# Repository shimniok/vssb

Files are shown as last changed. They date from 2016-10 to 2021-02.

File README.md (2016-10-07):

A Vehicle Speed Sensor Buffer (VSSB) for GM Throttle Body Injection (TBI) ECM on my 86 Jeep
Grand Wagoneer.

The Jeep GW uses a VSS for cruise control that outputs 8-pulse (8000 pulses/mile) sine wave
This circuit and firmware convert the OEM VSS signal to a 2-pulse square wave 5V signal
compatible with the GM TBI ECM ('7747) that I'm using.

It also outputs a 4-pulse signal which would be used (I think) by electronic GM speedos. 
The GW speedo, of course, is mechanical.

So what's the advantage of having a working speed sensor? At least a couple of TBI features
are enabled. The ECM is able to distinguish between idle mode (vehicle speed < 4mph) and
throttle-off coasting.  Additionally, Deceleration Fuel Cut-Off (DCFO) mode is enabled in
part based on speed.  And, if enabled, lean highway cruise is based on speed as well.

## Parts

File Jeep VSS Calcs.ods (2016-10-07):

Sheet: Sheet1
Jeep VSS Calculations
Pulses / mile | 8000
mph | 1 | 2 | 4 | 6 | 8 | 10 | 20 | 40 | 60 | 80 | 100
Pulses / sec | 2.2 | 4.4 | 8.9 | 13.3 | 17.8 | 22.2 | 44.4 | 88.9 | 133.3 | 177.8 | 222.2
Measurements | Freq | Ampl
 | 10.0 | 0.8
 | 14.3 | 1.0
 | 25.0 | 1.8 |  |  |  |  |  |  |  |  |  | Cutoff at 50hz with 1st order filter means ½ gain at 100hz
 | 62.5 | 2.2 |  |  |  |  |  |  |  |  |  | R | 220 | K
 |  |  |  |  |  |  |  |  |  |  |  | Freq | 50
 | div | ms/div | div | v/div | freq | vpp |  |  |  |  |  | C | 0.0145 | uF
 | 5 | 10 | 1.8 | 0.5 | 20.0 | 0.9
 | 4 | 10 | 2 | 0.5 | 25.0 | 1.0
 | 3 | 10 | 2.4 | 0.5 | 33.3 | 1.2
 | 2 | 10 | 4 | 0.5 | 50.0 | 2.0
 | 3 | 5 | 5.2 | 0.5 | 66.7 | 2.6
 | 2.6 | 5 | 6 | 0.5 | 76.9 | 3.0
 | 1.6 | 5 | 4 | 1 | 125.0 | 4.0

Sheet: Sheet2
Schmitt Trigger Op Amp
Vcc | 5 | V
R1 | 330.0 | KΩ
R2 | 330.0 | KΩ
RFB | 330.0 | KΩ
R1||RFB (high) | 165.0 | KΩ
R2||RFB (low) | 165.0 | KΩ
Vhigh | 3.33 | V | 66.67%
Vlow | 1.67 | V | 33.33%

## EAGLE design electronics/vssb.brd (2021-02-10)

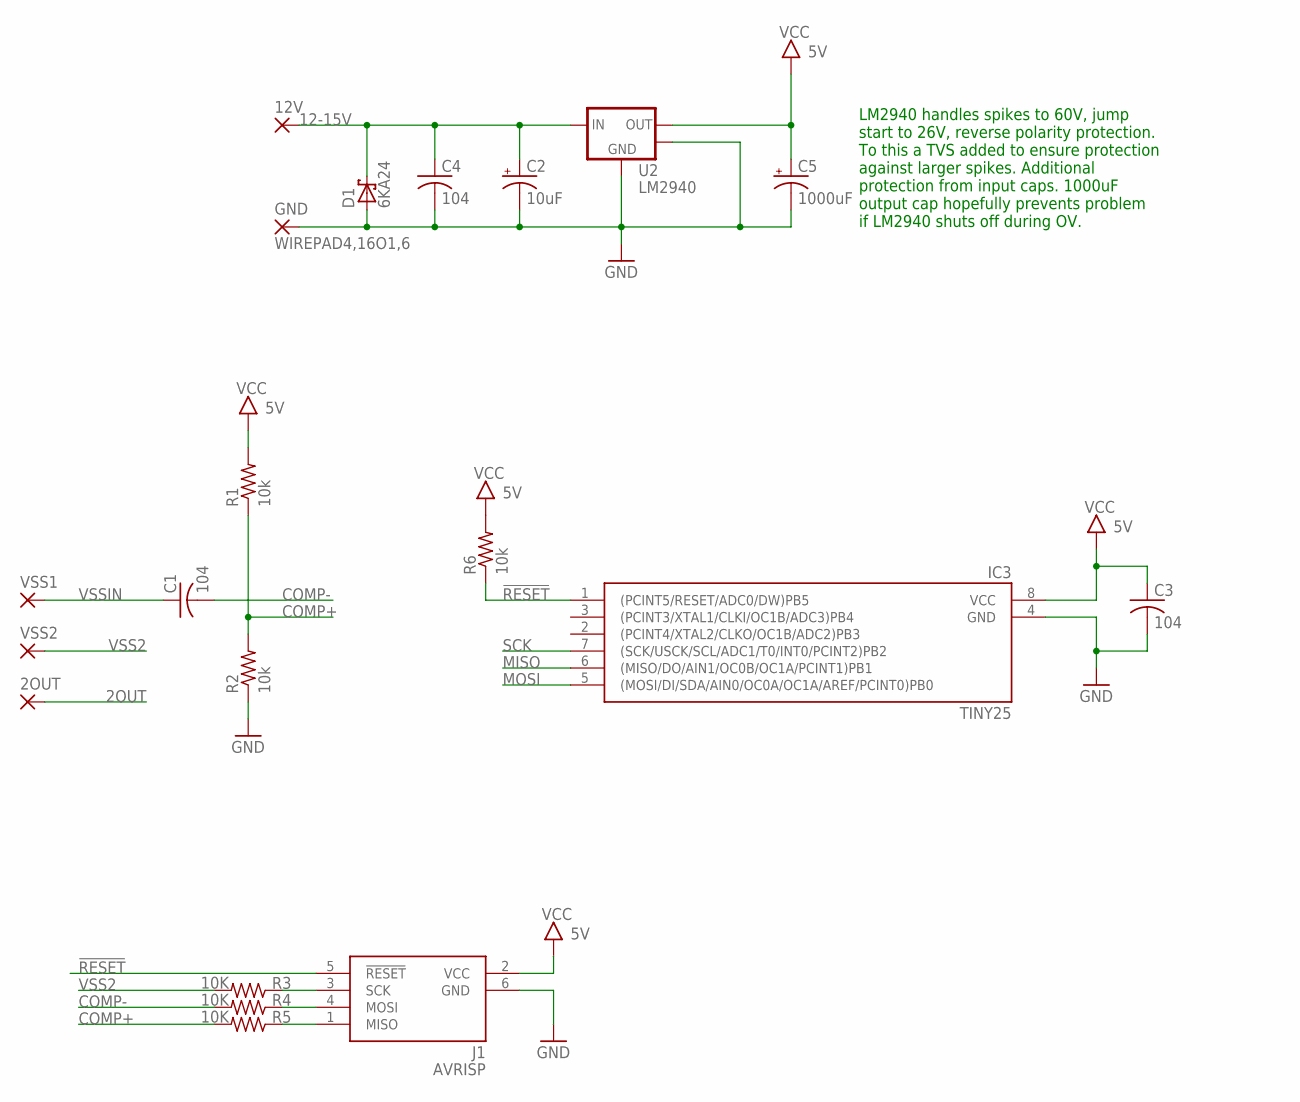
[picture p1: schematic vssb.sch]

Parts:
2OUT, 12V: WIREPAD4,16O1,6; 4,16O1,6
C1: 104; C050-024X044
C2: 10uF; E2,5-6
C3, C4: 104; C0603
C5: 1000uF; E5-13
D1: 6KA24; P600
GND: WIREPAD4,16O1,6; 4,16O1,6
IC3: TINY25; SOIC8N
J1: AVRISP; CON6P2R
R1, R2, R6: 10k; R0603
R3, R4, R5: 10K; R0603
U2: LM2940; SOT-223-3
VSS1, VSS2: WIREPAD4,16O1,6; 4,16O1,6

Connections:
2OUT: 2OUT.1
12-15V: 12V.1, C2.+, C4.1, D1.C, U2.1 (VIN)
!RESET: IC3.1 ((PCINT5/RESET/ADC0/DW)PB5), J1.5 (!RESET), R6.1
COMP+: R1.1, R2.2, R5.2
COMP-: C1.2, R4.2
GND: C2.-, C3.2, C4.2, C5.-, D1.A, GND.1, IC3.4 (GND), J1.6 (GND), R2.1, U2.2 (GND), U2.4 (TAB)
MISO: IC3.6 ((MISO/DO/AIN1/OC0B/OC1A/PCINT1)PB1), J1.1 (MISO), R5.1
MOSI: IC3.5 ((MOSI/DI/SDA/AIN0/OC0A/OC1A/AREF/PCINT0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), J1.4 (MOSI), R4.1
SCK: IC3.7 ((SCK/USCK/SCL/ADC1/T0/INT0/PCINT2)PB2), J1.3 (SCK), R3.1
VCC: C3.1, C5.+, IC3.8 (VCC), J1.2 (VCC), R1.2, R6.2, U2.3 (VOUT)
VSS2: R3.2, VSS2.1
VSSIN: C1.1, VSS1.1

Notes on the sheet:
LM2940 handles spikes to 60V, jump start to 26V, reverse polarity protection. To this a TVS added to ensure protection against larger spikes. Additional protection from input caps. 1000uF output cap hopefully prevents problem if LM2940 shuts off during OV.

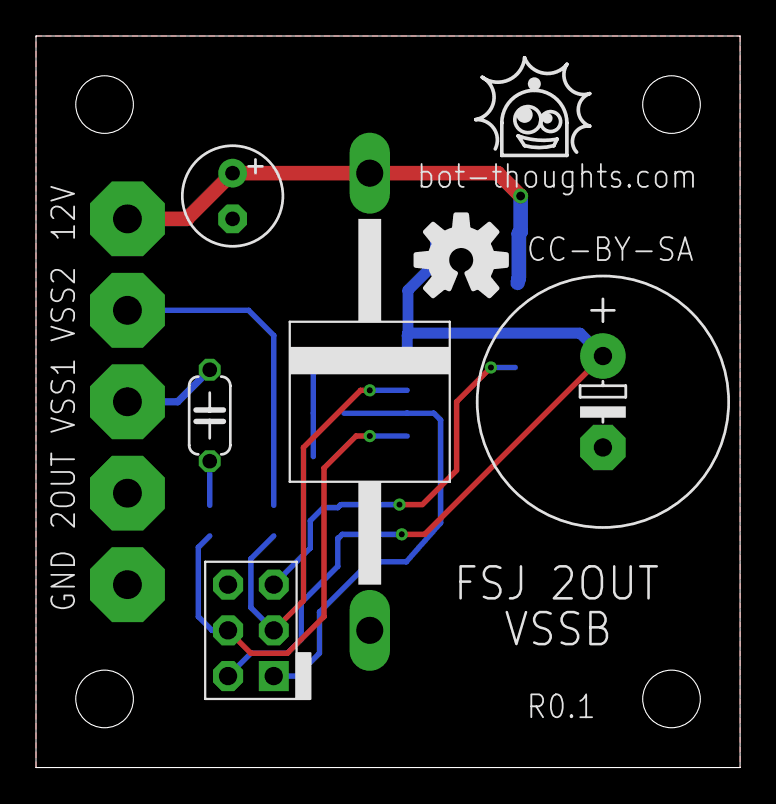
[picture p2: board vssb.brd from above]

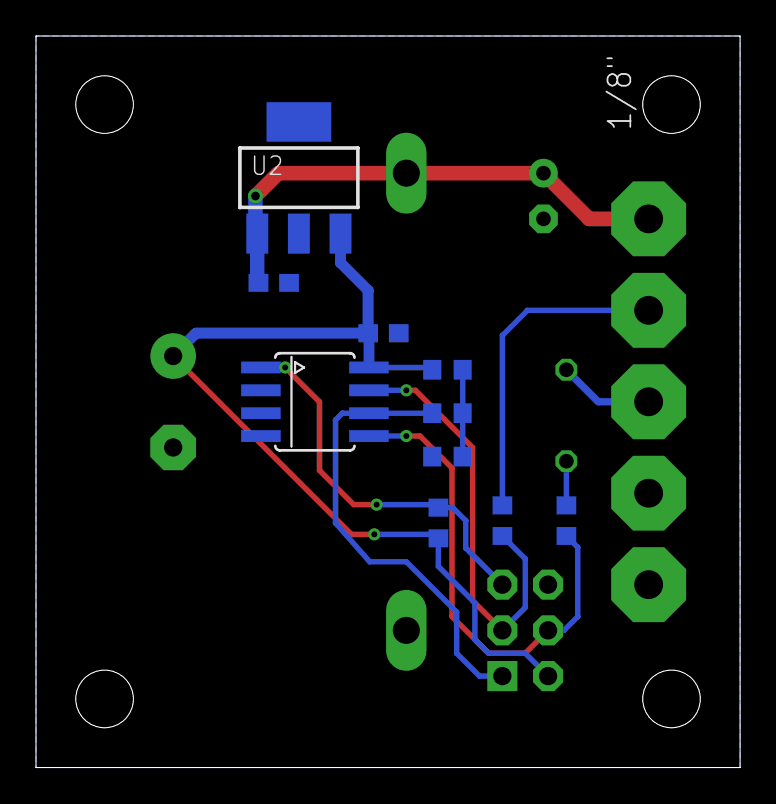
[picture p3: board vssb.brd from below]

Board: 2 copper layers, 39.1 x 40.6 mm, 20 parts (10 on the bottom side), 11 nets.

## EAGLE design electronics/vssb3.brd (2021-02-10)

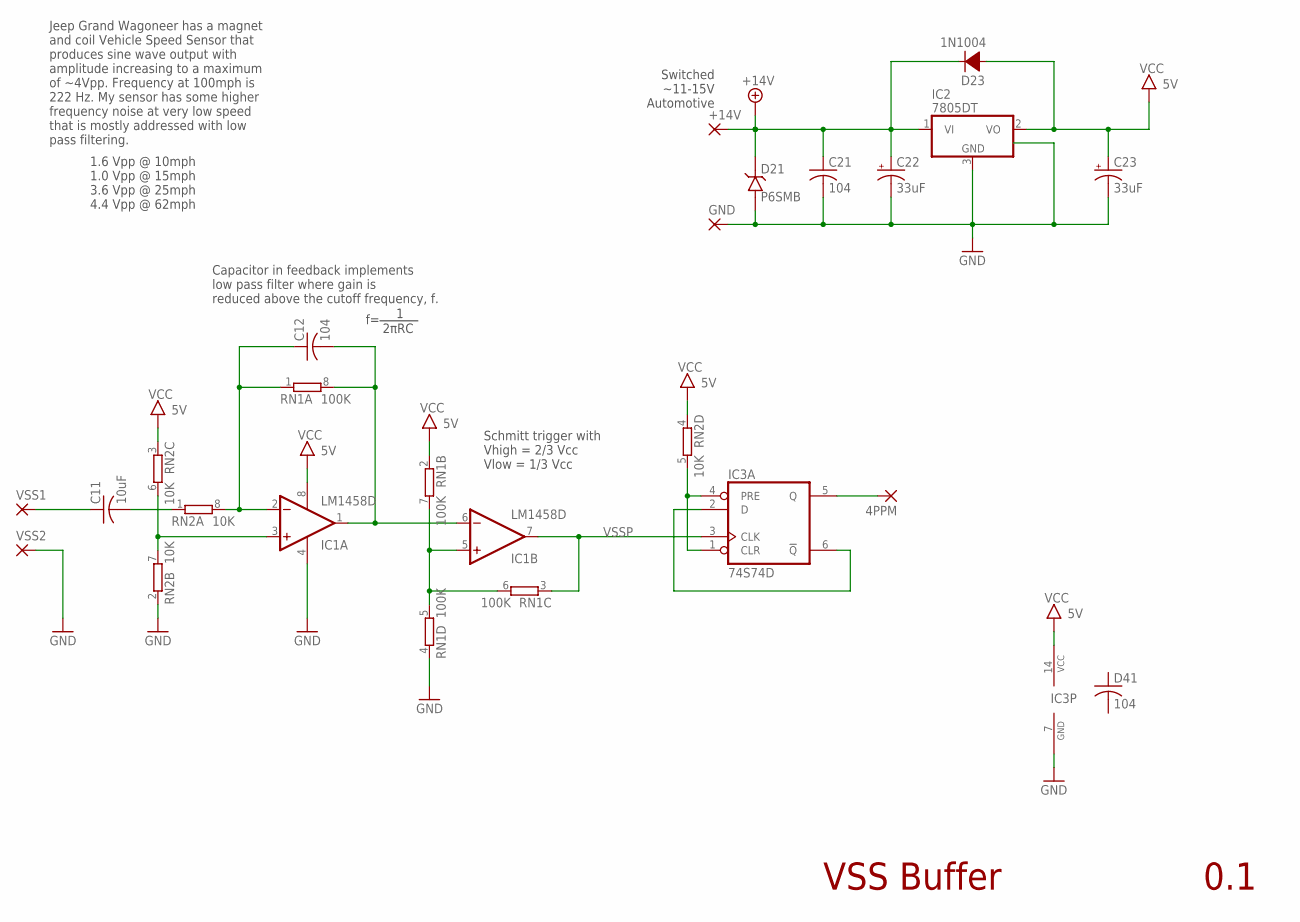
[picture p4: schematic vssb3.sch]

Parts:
4PPM: WIREPAD3,17/1,3; 3,17/1,3
+14V: WIREPAD3,17/1,3; 3,17/1,3
C11: 10uF; C1206
C12, C21: 104; C0603
C22, C23: 33uF; SMC_B
D21: P6SMB; DO-214AA
D23: 1N1004; SMA
D41: 104; C0603
GND: WIREPAD3,17/1,3; 3,17/1,3
IC1: LM1458D; SO08
IC2: 7805DT; TO252
IC3: 74S74D; SO14
RN1: 100K; EXB38V
RN2: 10K; EXB38V
VSS1, VSS2: WIREPAD3,17/1,3; 3,17/1,3

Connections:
4PPM: 4PPM.1, IC3.5 (Q)
+14V: +14V.1, C21.1, C22.+, D21.P$1 (C), D23.C, IC2.1 (VI)
GND: C21.2, C22.-, C23.-, D21.P$2 (A), GND.1, IC1.4 (V-), IC2.3 (GND), IC3.7 (GND), RN1.4 (1), RN2.2 (1), VSS2.1
unnamed: C11.2, RN2.1
unnamed: C12.1, IC1.2 (-IN), RN1.1, RN2.8 (2)
unnamed: IC1.3 (+IN), RN2.6 (2), RN2.7 (2)
unnamed: IC1.5 (+IN), RN1.5 (2), RN1.6 (2), RN1.7 (2)
unnamed: IC3.2 (D), IC3.6 (!Q)
unnamed: IC3.1 (CLR), IC3.4 (PRE), RN2.5 (2)
OUT1: C12.2, IC1.1 (OUT), IC1.6 (-IN), RN1.8 (2)
VCC: C23.+, D23.A, IC1.8 (V+), IC2.2 (VO), IC3.14 (VCC), RN1.2 (1), RN2.3 (1), RN2.4 (1)
VSS1: C11.1, VSS1.1
VSSP: IC1.7 (OUT), IC3.3 (CLK), RN1.3 (1)

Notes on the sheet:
Switched ~11-15V Automotive
Jeep Grand Wagoneer has a magnet and coil Vehicle Speed Sensor that produces sine wave output with amplitude increasing to a maximum of ~4Vpp. Frequency at 100mph is 222 Hz. My sensor has some higher frequency noise at very low speed that is mostly addressed with low pass filtering.
1.6 Vpp @ 10mph 1.0 Vpp @ 15mph 3.6 Vpp @ 25mph 4.4 Vpp @ 62mph
Capacitor in feedback implements low pass filter where gain is reduced above the cutoff frequency, f.
Schmitt trigger with Vhigh = 2/3 Vcc Vlow = 1/3 Vcc
2πRC
VSS Buffer
0.1

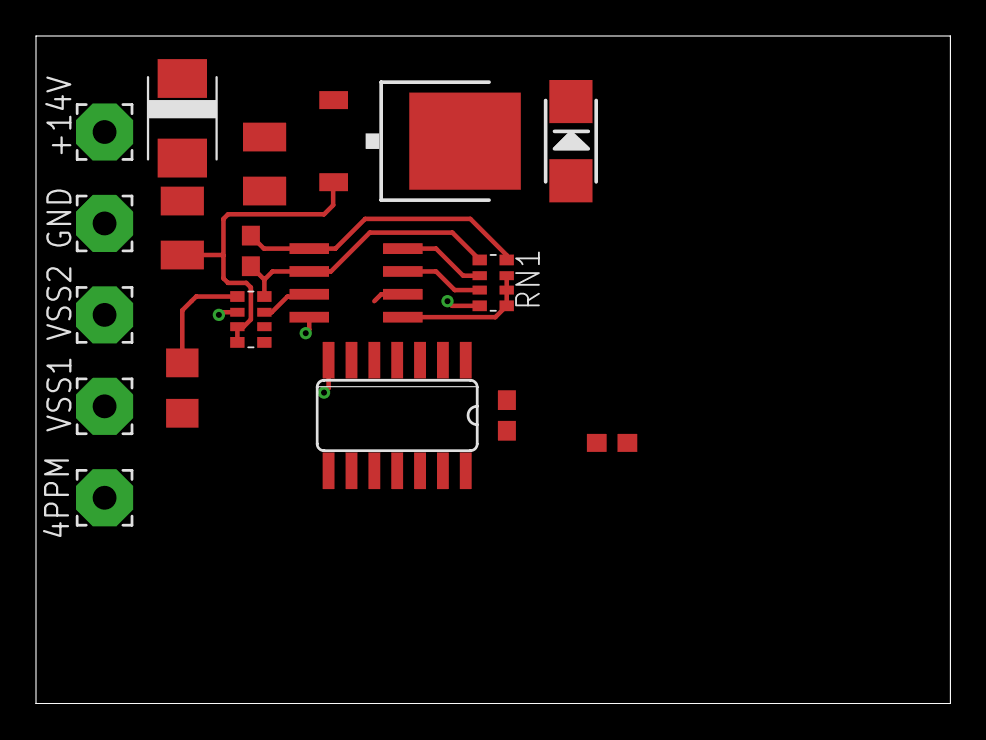
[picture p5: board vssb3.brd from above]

Board: 2 copper layers, 50.8 x 37.1 mm, 18 parts (0 on the bottom side), 13 nets.

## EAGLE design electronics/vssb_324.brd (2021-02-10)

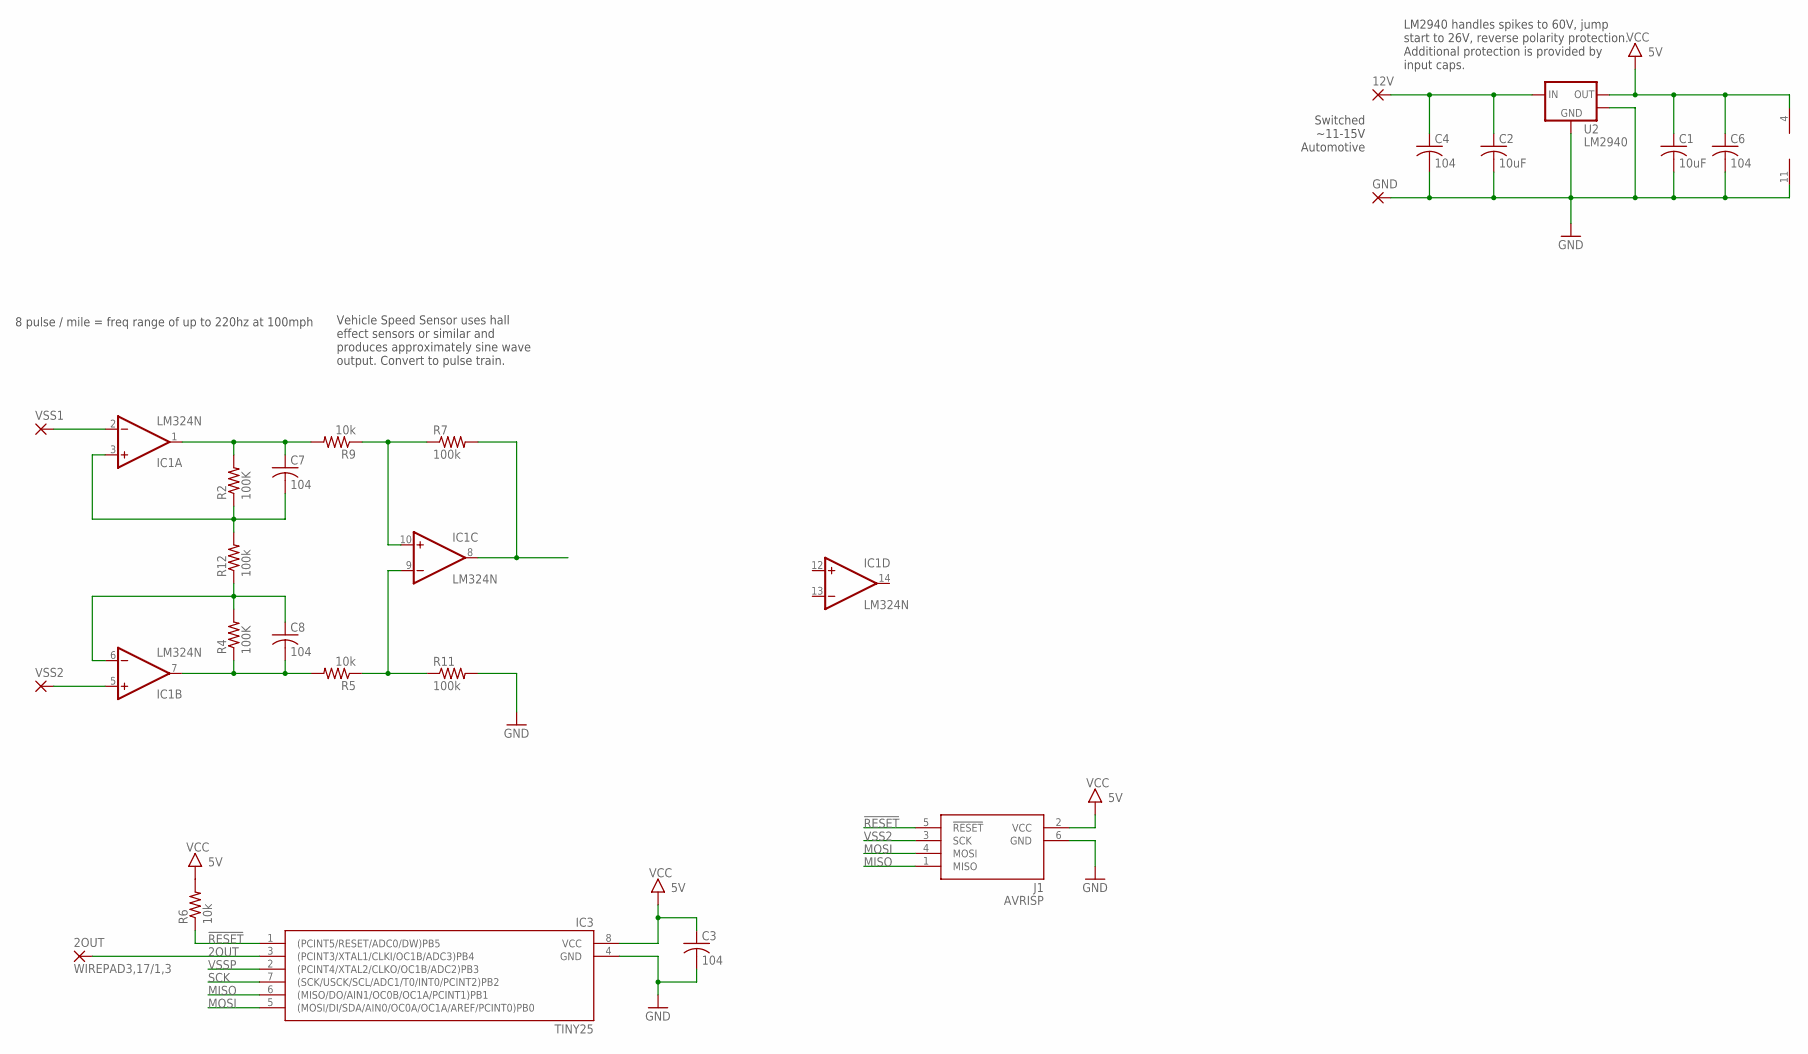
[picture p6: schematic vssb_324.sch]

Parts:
2OUT, 12V: WIREPAD3,17/1,3; 3,17/1,3
C1, C2: 10uF; C1206
C3, C4, C6, C7, C8: 104; C0603
GND: WIREPAD3,17/1,3; 3,17/1,3
IC1: LM324N; DIL14
IC3: TINY25; DIL08
J1: AVRISP; CON6P2R
R2, R4: 100K; R0603
R5, R6, R9: 10k; R0603
R7, R11, R12: 100k; R0603
U2: LM2940; TO263-3
VSS1, VSS2: WIREPAD3,17/1,3; 3,17/1,3

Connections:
2OUT: 2OUT.1, IC3.3 ((PCINT3/XTAL1/CLKI/OC1B/ADC3)PB4)
12-15V: 12V.1, C2.1, C4.1, U2.1 (VIN)
!RESET: IC3.1 ((PCINT5/RESET/ADC0/DW)PB5), J1.5 (!RESET), R6.1
GND: C1.2, C2.2, C3.2, C4.2, C6.2, GND.1, IC1.11 (V-), IC3.4 (GND), J1.6 (GND), R11.2, U2.2 (GND), U2.4 (TAB)
MISO: IC3.6 ((MISO/DO/AIN1/OC0B/OC1A/PCINT1)PB1), J1.1 (MISO)
MOSI: IC3.5 ((MOSI/DI/SDA/AIN0/OC0A/OC1A/AREF/PCINT0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), J1.4 (MOSI)
unnamed: C8.1, IC1.6 (-IN), R4.2, R12.1
unnamed: C7.2, IC1.3 (+IN), R2.1, R12.2
unnamed: IC1.8 (OUT), R7.2
unnamed: C7.1, IC1.1 (OUT), R2.2, R9.2
unnamed: C8.2, IC1.7 (OUT), R4.1, R5.2
unnamed: IC1.10 (+IN), R7.1, R9.1
unnamed: IC1.9 (-IN), R5.1, R11.1
SCK: IC3.7 ((SCK/USCK/SCL/ADC1/T0/INT0/PCINT2)PB2)
VCC: C1.1, C3.1, C6.1, IC1.4 (V+), IC3.8 (VCC), J1.2 (VCC), R6.2, U2.3 (VOUT)
VSS1: IC1.2 (-IN), VSS1.1
VSS2: IC1.5 (+IN), J1.3 (SCK), VSS2.1
VSSP: IC3.2 ((PCINT4/XTAL2/CLKO/OC1B/ADC2)PB3)

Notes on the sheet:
LM2940 handles spikes to 60V, jump start to 26V, reverse polarity protection. Additional protection is provided by input caps.
Switched ~11-15V Automotive
Vehicle Speed Sensor uses hall effect sensors or similar and produces approximately sine wave output. Convert to pulse train.
8 pulse / mile = freq range of up to 220hz at 100mph

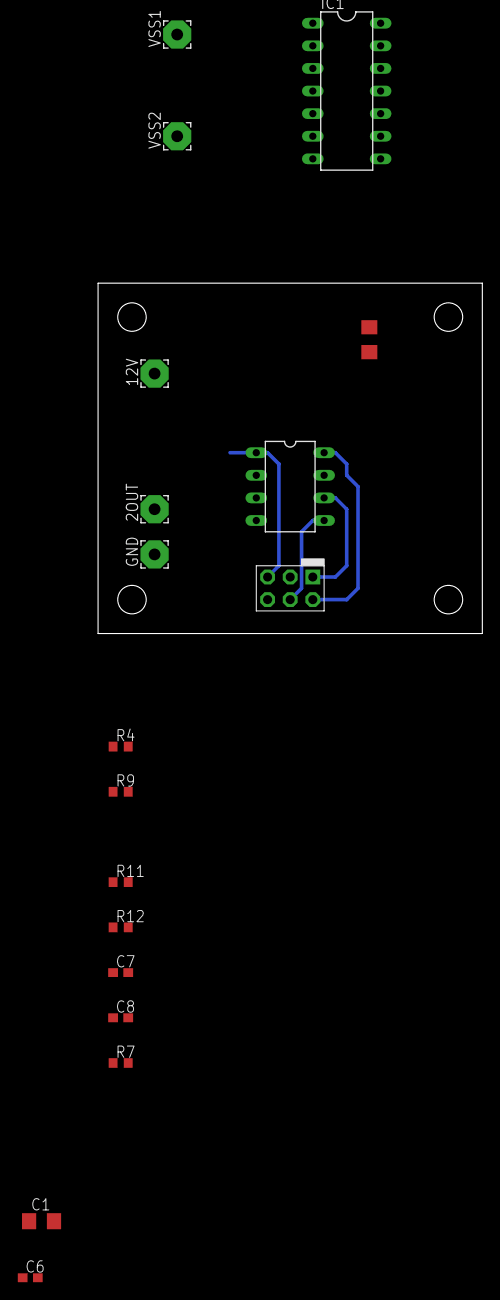
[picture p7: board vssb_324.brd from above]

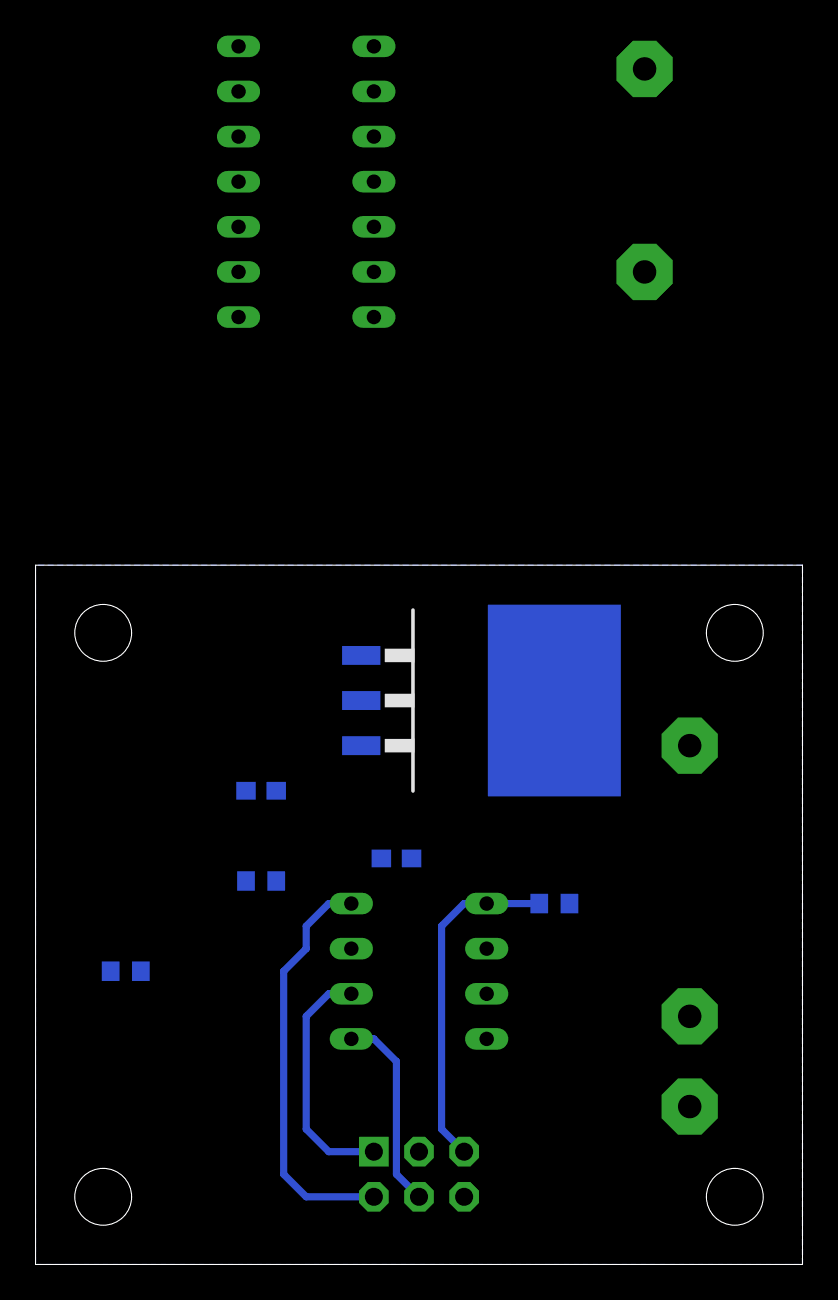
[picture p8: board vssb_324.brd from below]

Board: 2 copper layers, 43.2 x 39.4 mm, 24 parts (6 on the bottom side), 16 nets.

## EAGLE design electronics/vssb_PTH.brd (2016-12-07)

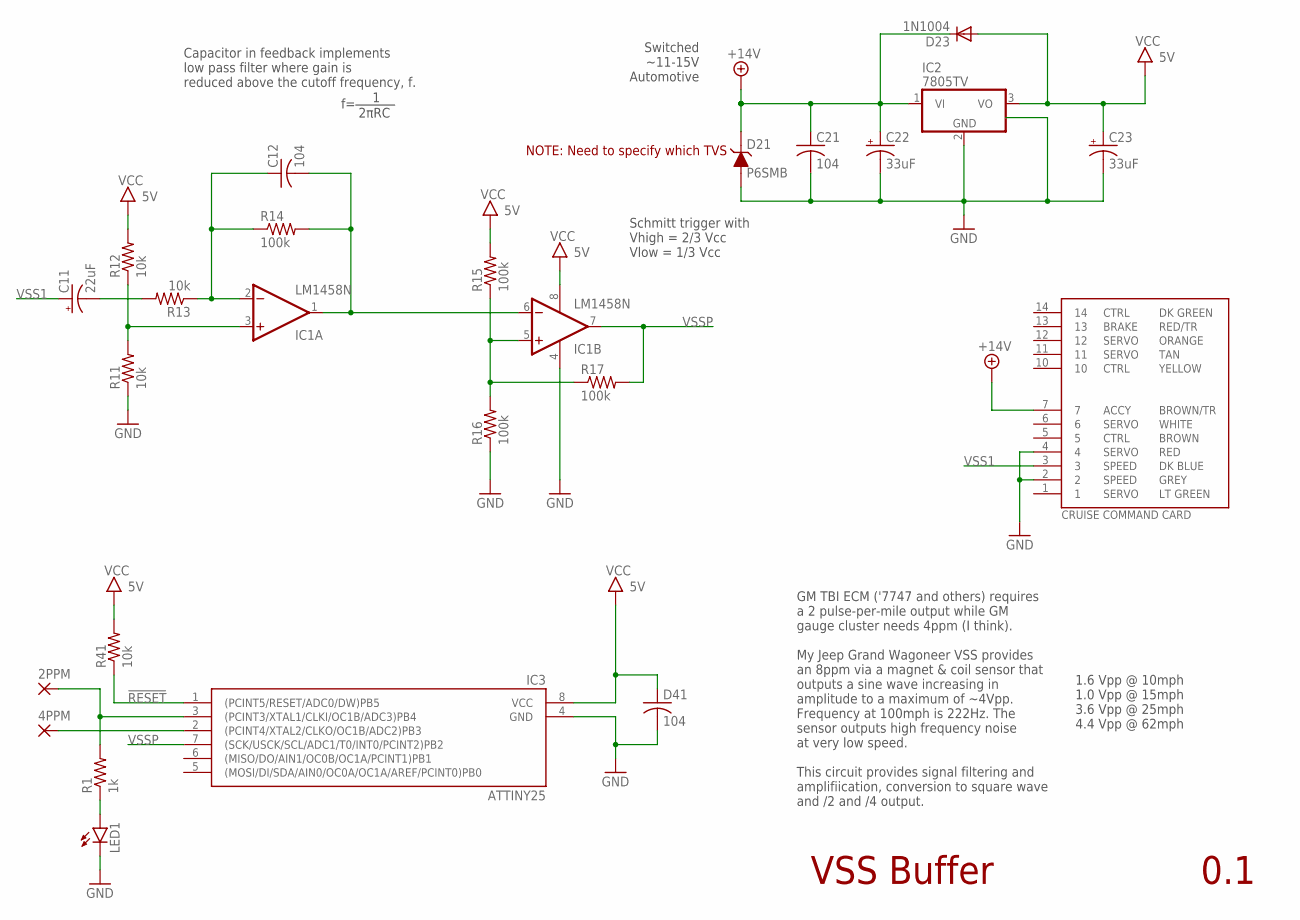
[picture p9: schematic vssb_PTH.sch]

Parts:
2PPM, 4PPM: WIREPAD3,17/1,3; 3,17/1,3
C11: 22uF; E5-5
C12, C21: 104; C050-024X044
C22, C23: 33uF; E2,5-6
D21: P6SMB; DO-214AA
D23: 1N1004; DO41-10
D41: 104; C050-024X044
IC1: LM1458N; DIL08
IC2: 7805TV; TO220V
IC3: ATTINY25; DIL08
LED1: LED3MM
R1: 1k; 0204/5
R11, R12, R13, R41: 10k; 0204/5
R14, R15, R16, R17: 100k; 0204/5
U$4: FSJ_CC_CARD; FSJ_CC

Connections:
!RESET: IC3.1 ((PCINT5/RESET/ADC0/DW)PB5), R41.1
+14V: C21.1, C22.+, D21.P$1 (C), D23.C, IC2.1 (VI), U$4.7
/2: 2PPM.1, IC3.3 ((PCINT3/XTAL1/CLKI/OC1B/ADC3)PB4), R1.2
GND: C21.2, C22.-, C23.-, D21.P$2 (A), D41.2, IC1.4 (V-), IC2.2 (GND), IC3.4 (GND), LED1.K (C), R11.1, R16.1, U$4.2, U$4.4
unnamed: C11.-, R13.2
unnamed: C12.1, IC1.2 (-IN), R13.1, R14.1
unnamed: IC1.3 (+IN), R11.2, R12.1
unnamed: IC1.5 (+IN), R15.1, R16.2, R17.1
unnamed: LED1.A, R1.1
unnamed: 4PPM.1, IC3.2 ((PCINT4/XTAL2/CLKO/OC1B/ADC2)PB3)
OUT1: C12.2, IC1.1 (OUT), IC1.6 (-IN), R14.2
VCC: C23.+, D23.A, D41.1, IC1.8 (V+), IC2.3 (VO), IC3.8 (VCC), R12.2, R15.2, R41.2
VSS1: C11.+, U$4.3
VSSP: IC1.7 (OUT), IC3.7 ((SCK/USCK/SCL/ADC1/T0/INT0/PCINT2)PB2), R17.2

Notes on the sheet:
Switched ~11-15V Automotive
1.6 Vpp @ 10mph 1.0 Vpp @ 15mph 3.6 Vpp @ 25mph 4.4 Vpp @ 62mph
Capacitor in feedback implements low pass filter where gain is reduced above the cutoff frequency, f.
Schmitt trigger with Vhigh = 2/3 Vcc Vlow = 1/3 Vcc
2πRC
VSS Buffer
0.1
GM TBI ECM ('7747 and others) requires a 2 pulse-per-mile output while GM gauge cluster needs 4ppm (I think). My Jeep Grand Wagoneer VSS provides an 8ppm via a magnet & coil sensor that outputs a sine wave increasing in amplitude to a maximum of ~4Vpp. Frequency at 100mph is 222Hz. The sensor outpu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
NOTE: Need to specify which TVS

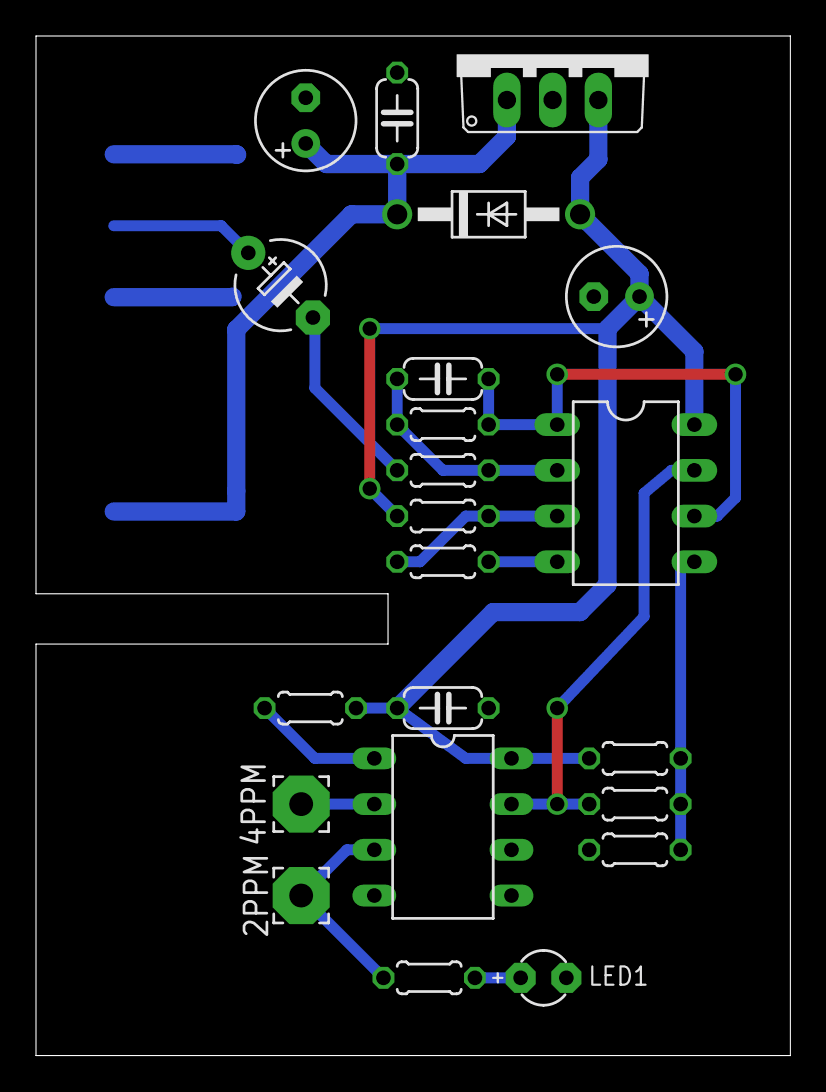
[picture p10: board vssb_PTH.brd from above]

Board: 2 copper layers, 41.9 x 56.6 mm, 24 parts (1 on the bottom side), 14 nets.

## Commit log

2016-10-07 initial release
    [Jeep VSS Calcs.ods, vssb_PTH.brd, vssb_PTH.sch]
2016-10-10 minor tweaks to 1458 power, tvs symbol
    [vssb_PTH.sch]
2016-10-11 ground plane; minor layout moves for some capacitors and regulator, reroute, shrunk board width
    [vssb_PTH.brd, vssb_PTH.sch]
2016-10-11 shrunk card edge and board width
    [vssb_PTH.brd, vssb_PTH.sch]
2016-12-07 Changed input series cap to 22uF based on experimentation
    [vssb_PTH.brd, vssb_PTH.sch]
2016-12-07 configured output ports to start high (to light LEDs); removed commented sleep statements in main while infinite loop
2021-02-10 added additional versions of board/schematic
    [vssb.brd, vssb.sch, vssb3.brd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]

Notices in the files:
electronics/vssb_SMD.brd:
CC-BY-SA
